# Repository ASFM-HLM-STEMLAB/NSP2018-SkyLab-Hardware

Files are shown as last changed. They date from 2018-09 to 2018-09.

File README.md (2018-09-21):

# NSP2018-SkyLab-Hardware
ASFM Near Space Program 2018 - SkyLab FlightComputer Hardware

## Welcome to NSP2018-SkyLab-Hardware repository
The flight computer consists of a *ESP32* Microcontroller in the Adafruit Feather form factor. 
[ESP32](https://www.adafruit.com/product/3405)

* Optionally we are waiting for Particle.io to release their new mesh line of MCUs. We love the development environment from Particle.io and their devices. For now we are awaiting for them to release the line, we should test compatibility when they do and hope for the best.<small>

This device contains an onboard GPS, LoRa Radio, SDCard and Internal Pressure and Temp Sensor. It is designed to interface with an optional external Iridium RockBlock Satelite Module:
[RockBlock Sat Modem](https://www.sparkfun.com/products/14498)

Also contains ports for external sensors, both in i2c and SPI. It also has a couple of mosfets for a buzzer and a beacon or optionally an electric match to prevent floaters.

See the attached BOM for details

The internal GPS is a U-Blox GPS picked because it allows the device to be effective above the 60,000ft gps limit.

Designed in Autodesk Eagle.
by: Francisco Lobo
at ASFM STEM LAB Monterrey
[HLM STEM-LAB Instagram](https://www.instagram.com/asfmstemlab/)

=======

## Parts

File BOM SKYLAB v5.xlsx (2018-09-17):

SKY LAB V5.0 - HIGH ALTITUDE BALOON MAIN COMPUTER (BOM)
https://github.com/ASFM-HLM-STEMLAB/skylab
Revision 5 | Sept 17 2018
Part | Value | Package | Part. No. | Description | PROD_ID | DigiKey URL
R3 | 10 | 603 | MCT06030C1009FP500 | Resistor |  | https://www.digikey.com/product-detail/en/vishay-beyschlag/MCT06030C1009FP500/MCT0603-10.0-CFTR-ND/2607826
R13 | 220 | M0805 | ERJ-PB6D2200V | RESISTOR, American symbol |  | https://www.digikey.com/product-detail/en/panasonic-electronic-components/ERJ-PB6D2200V/P20941TR-ND/6213724
R9 | 330 | M0805 | P330CDKR-ND | RESISTOR, American symbol |  | https://www.digikey.com/product-detail/en/panasonic-electronic-components/ERJ-6ENF3300V/P330CDKR-ND/1747213
R10 | 330 | M0805 | P330CDKR-ND | RESISTOR, American symbol |  | https://www.digikey.com/product-detail/en/panasonic-electronic-components/ERJ-6ENF3300V/P330CDKR-ND/1747213
R11 | 330 | M0805 | P330CDKR-ND | RESISTOR, American symbol |  | https://www.digikey.com/product-detail/en/panasonic-electronic-components/ERJ-6ENF3300V/P330CDKR-ND/1747213
R12 | 330 | M0805 | P330CDKR-ND | RESISTOR, American symbol |  | https://www.digikey.com/product-detail/en/panasonic-electronic-components/ERJ-6ENF3300V/P330CDKR-ND/1747213
C1 | 0.1uF | 603 | CC0603ZRY5V9BB104 | 0.1¬µF ceramic capacitors | CAP-00810 | https://www.digikey.com/product-detail/en/yageo/CC0603ZRY5V9BB104/311-1343-1-ND/2103127
C2 | 0.1uF | 603 | CC0603ZRY5V9BB104 | 0.1¬µF ceramic capacitors | CAP-00810 | https://www.digikey.com/product-detail/en/yageo/CC0603ZRY5V9BB104/311-1343-1-ND/2103127
C5 | 0.1uF | 603 | CC0603ZRY5V9BB104 | 0.1¬µF ceramic capacitors | CAP-00810 | https://www.digikey.com/product-detail/en/yageo/CC0603ZRY5V9BB104/311-1343-1-ND/2103127
C6 | 0.1uF | 603 | CC0603ZRY5V9BB104 | 0.1¬µF ceramic capacitors | CAP-00810 | https://www.digikey.com/product-detail/en/yageo/CC0603ZRY5V9BB104/311-1343-1-ND/2103127
C4 | 10uF | 1206 | CL31A106KPHNNNE | 10.0¬µF ceramic capacitors | CAP-10057 | https://www.digikey.com/product-detail/en/samsung-electro-mechanics/CL31A106KPHNNNE/1276-1148-1-ND/3889234
R8 | 220K | 805 | KTR10EZPF2203 | 0.22Œ© resistor | RES-09883 | https://www.digikey.com/product-detail/en/rohm-semiconductor/KTR10EZPF2203/RHM220KAHCT-ND/1983969
R14 | 220K | 805 | KTR10EZPF2203 | 0.22Œ© resistor | RES-09883 | https://www.digikey.com/product-detail/en/rohm-semiconductor/KTR10EZPF2203/RHM220KAHCT-ND/1983969
C8 | 22uF | 805 | CL21A226KPCLRNC | 22¬µF ceramic capacitors | CAP-08402 | https://www.digikey.com/product-detail/en/samsung-electro-mechanics/CL21A226KPCLRNC/1276-6786-6-ND/5962020
D3 | 250mA/100V | SOD-323 | 1N4148WSF | Diode 250mA/100V | DIO-09646 | https://www.digikey.com/product-detail/en/diodes-incorporated/1N4148WSF-7/1N4148WSF-7DICT-ND/7605263
R7 | 2M | 805 | RC0805FR-072ML | 0.22Œ© resistor | RES-09883 | https://www.digikey.com/product-detail/en/yageo/RC0805FR-072ML/311-2.00MCRCT-ND/730612
R15 | 2M | 805 | RC0805FR-072ML | 0.22Œ© resistor | RES-09883 | https://www.digikey.com/product-detail/en/yageo/RC0805FR-072ML/311-2.00MCRCT-ND/730612
C3 | 330uF | EIA6032 | TPSC337K006R0080 | Capacitor Polarized |  | https://www.digikey.com/product-detail/en/TPSC337K006R0080/478-11108-1-ND/7536284
L1 | 33nH | 603 | LQW18AN33NJ00D | Inductors |  | https://www.digikey.com/product-detail/en/murata-electronics-north-america/LQW18AN33NJ00D/490-1175-1-ND/584620
R1 | 4.7K | M0805 | ESR10EZPJ472 | RESISTOR, American symbol |  | https://www.digikey.com/product-detail/en/rohm-semiconductor/ESR10EZPJ472/RHM4.7KKCT-ND/1763028
R2 | 4.7K | M0805 | ESR10EZPJ472 | RESISTOR, American symbol |  | https://www.digikey.com/product-detail/en/rohm-semiconductor/ESR10EZPJ472/RHM4.7KKCT-ND/1763028
R4 | 4.7K | M0805 | ESR10EZPJ472 | RESISTOR, American symbol |  | https://www.digikey.com/product-detail/en/rohm-semiconductor/ESR10EZPJ472/RHM4.7KKCT-ND/1763028
R5 | 4.7K | M0805 | ESR10EZPJ472 | RESISTOR, American symbol |  | https://www.digikey.com/product-detail/en/rohm-semiconductor/ESR10EZPJ472/RHM4.7KKCT-ND/1763028
R6 | 4.7K | M0805 | ESR10EZPJ472 | RESISTOR, American symbol |  | https://www.digikey.com/product-detail/en/rohm-semiconductor/ESR10EZPJ472/RHM4.7KKCT-ND/1763028
R16 | 4.7K | M0805 | ESR10EZPJ472 | RESISTOR, American symbol |  | https://www.digikey.com/product-detail/en/rohm-semiconductor/ESR10EZPJ472/RHM4.7KKCT-ND/1763028
L2 | 4.7uH 1.2A | 603 | MBKK1608T4R7M | Inductors |  | https://www.digikey.com/product-detail/en/taiyo-yuden/MBKK1608T4R7M/587-4152-1-ND/5035312
Q2 | 5.8A/30V/35mŒ | SOT23-3 | SSM3K333R,LF | N-channel MOSFETs | TRANS-12988 | https://www.digikey.com/product-detail/en/toshiba-semiconductor-and-storage/SSM3K333RLF/SSM3K333RLFCT-ND/3522391
Q1 | 500mA/300V | SOT23-3 | ZXTN19020DFFTA | NPN transistor | TRANS-09116 | https://www.digikey.com/product-detail/en/diodes-incorporated/ZXTN19020DFFTA/ZXTN19020DFFCT-ND/1557774
BT1 | 6.8MM_CELL | BATT-6.8MM | MS621FE-FL11E | Battery - Single Cell | BATT-13734 | https://www.digikey.com/product-detail/en/seiko-instruments/MS621FE-FL11E/728-1057-ND/1889208
U2 | BME680 | LGA3.0X3.0 | BME680 | BME 680 - Sensor |  | https://www.digikey.com/product-detail/en/bosch-sensortec/BME680/828-1077-1-ND/7401321
LED | Green | LED-1206 | LTST-C150GKT‎ | LED (Generic) |  | https://www.digikey.com/product-detail/en/lite-on-inc/LTST-C150GKT/160-1169-1-ND/269241
LED | Green | LED-1206 | LTST-C150GKT‎ | LED (Generic) |  | https://www.digikey.com/product-detail/en/lite-on-inc/LTST-C150GKT/160-1169-1-ND/269241
LED | Green | LED-1206 | LTST-C150GKT‎ | LED (Generic) |  | https://www.digikey.com/product-detail/en/lite-on-inc/LTST-C150GKT/160-1169-1-ND/269241
LED | Green | LED-1206 | LTST-C150GKT‎ | LED (Generic) |  | https://www.digikey.com/product-detail/en/lite-on-inc/LTST-C150GKT/160-1169-1-ND/269241
J2 | SD_SOCKET | SD_SOCKET | 5031821852 | microSD Socket for Transflash | CONN-07820 | https://www.digikey.com/product-detail/en/molex-llc/5031821852/WM12834CT-ND/5823232
RADIO | RFM95W | RFM95W | RFM95W-915S2-ND | LoRA Radio |  | https://www.digikey.com/product-detail/en/rf-solutions/RFM95W-915S2/RFM95W-915S2-ND/6564923
GPS_ANT | SMA_EDGE | SMA-EDGE | 132255RP | SMA Antenna Connector |  | https://www.digikey.com/product-detail/en/amphenol-rf-division/132255RP/ACX1425-ND/1989874
RDIO_ANT | SMA_EDGE | SMA-EDGE | CON-SMA-EDGE-S | SMA Antenna Connector |  | https://www.digikey.com/product-detail/en/rf-solutions/CON-SMA-EDGE-S/CON-SMA-EDGE-S-ND/5845767
U1 | TPS61200 | QFN-10_PAD | TPS61200DRCT | DC to DC Booster | IC-10035 | https://www.digikey.com/product-detail/en/texas-instruments/TPS61200DRCT/296-21663-1-ND/1534252
UBLOX | UBLOX_MAX | UBLOX_MAX | MAX-M8W-0 | UBLOX MAX |  | https://www.digikey.com/product-detail/en/u-blox-america-inc/MAX-M8W-0/672-1004-1-ND/6150667
J1 |  | JST-2-SMD | S2B-PH-SM4-TB(LF)(SN) | JST 2MM MALE RA CONNECTOR | CONN-11443 | https://www.digikey.com/product-detail/en/jst-sales-america-inc/S2B-PH-SM4-TB-LF-SN/455-1749-1-ND/926846
S1 |  | SWTCH | PCM12SMTR | Single Pole, Double Throw (SPDT) Switch | SWCH-10651 | https://www.digikey.com/product-detail/en/c-k/PCM12SMTR/401-2016-1-ND/1640125

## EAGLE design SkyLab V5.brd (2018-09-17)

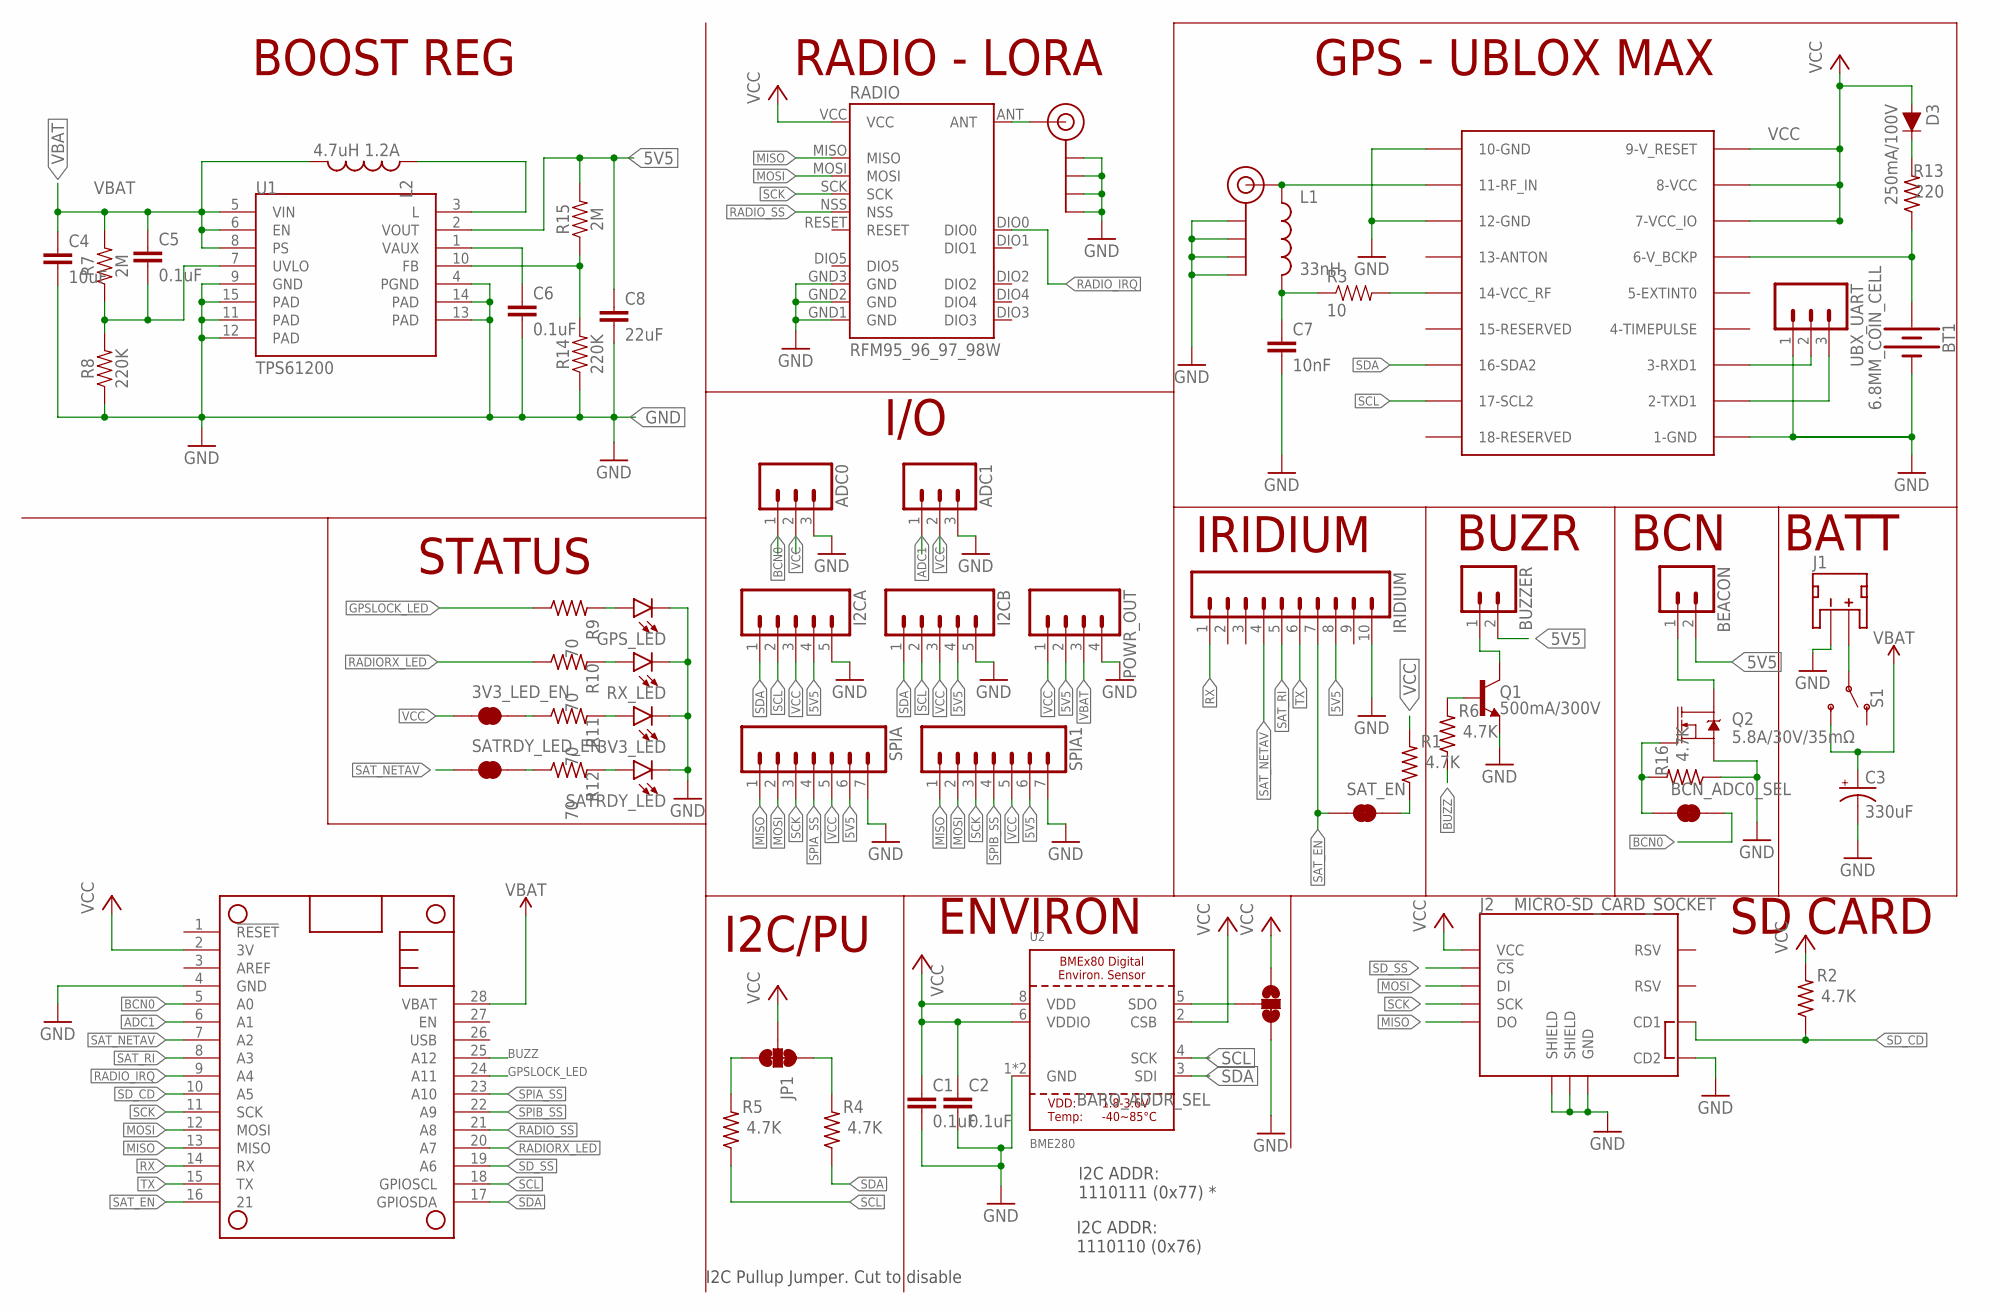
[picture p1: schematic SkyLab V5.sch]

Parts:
3V3_LED: LED1206; LED-1206
3V3_LED_EN: JUMPER-SMT_2_NC_TRACE_SILK; SMT-JUMPER_2_NC_TRACE_SILK
ADC0, ADC1: CONN_03; 1X03
BARO_ADDR_SEL: JUMPER-SMT_3_1-NC_TRACE_SILK; SMT-JUMPER_3_1-NC_TRACE_SILK
BCN_ADC0_SEL: JUMPER-SMT_2_NC_TRACE_SILK; SMT-JUMPER_2_NC_TRACE_SILK
BEACON: CONN_02; 1X02
BT1: 6.8MM_COIN_CELL; BATTCON-6.8MM
BUZZER: CONN_02; 1X02
C1, C2, C5, C6: 0.1uF; 0603
C3: 330uF; EIA6032
C4: 10uF; 1206
C7: 10nF; 0603
C8: 22uF; 0805
D3: 250mA/100V; SOD-323
GPS_ANT: SMA_EDGE; SMA-EDGE
GPS_LED: LED1206; LED-1206
I2CA, I2CB: CONN_05; 1X05
IRIDIUM: CONN_10"; 1X10
J1: JST_2MM_MALE; JST-2-SMD
J2: MICRO-SD_CARD_SOCKET; MICRO-SD-SOCKET
JP1: JUMPER-SMT_3_2-NC_TRACE_SILK; SMT-JUMPER_3_2-NC_TRACE_SILK
L1: 33nH; 0603
L2: 4.7uH 1.2A; 0603
MS1: FEATHERWING_NODIM; FEATHERWING_DIM
POWR_OUT: CONN_04; 1X04
Q1: 500mA/300V; SOT23-3
Q2: 5.8A/30V/35mΩ; SOT23-3
R1, R2, R4, R5, R6, R16: 4.7K; M0805
R3: 10; 0603-RES
R7, R15: 2M; 0805
R8, R14: 220K; 0805
R9, R10, R11, R12: 70; M0805
R13: 220; M0805
RADIO: RFM95_96_97_98W
RDIO_ANT: SMA_EDGE; SMA-EDGE
RX_LED: LED1206; LED-1206
S1: SWITCH-SPDT-SMD-RIGHT-ANGLE; SWITCH_SPST_SMD_A
SATRDY_LED: LED1206; LED-1206
SATRDY_LED_EN: JUMPER-SMT_2_NC_TRACE_SILK; SMT-JUMPER_2_NC_TRACE_SILK
SAT_EN: JUMPER-SMT_2_NC_TRACE_SILK; SMT-JUMPER_2_NC_TRACE_SILK
SPIA, SPIA1: CONN_07; 1X07
U1: TPS61200; QFN-10_PAD
U2: BME280
UBLOX: UBLOX_MAX
UBX_UART: CONN_03; 1X03

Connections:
5V5: BEACON.2, BUZZER.2, C8.1, I2CA.4, I2CB.4, IRIDIUM.8, POWR_OUT.2, R15.2, SPIA.6, SPIA1.6, U1.2 (VOUT)
ADC1: ADC1.1, MS1.6 (A1)
BCN0: ADC0.1, BCN_ADC0_SEL.2, MS1.5 (A0)
BUZZ: MS1.25 (A12), R6.1
EDITINF: BCN_ADC0_SEL.1, Q2.1 (G), R16.2
GND: 3V3_LED.C, ADC0.3, ADC1.3, BARO_ADDR_SEL.3, BT1.-, C1.2, C2.2, C3.P$2 (-), C4.2, C6.2, C7.2, C8.2, GPS_ANT.GND@0 (GND), GPS_ANT.GND@1 (GND), GPS_ANT.GND@2 (GND), GPS_ANT.GND@3 (GND), GPS_LED.C, I2CA.5, I2CB.5, IRIDIUM.10, J1.1 (-), J2.CD2, J2.GND, J2.GND1 (SHIELD), J2.GND3 (SHIELD), MS1.4 (GND), POWR_OUT.4, Q1.2 (E), Q2.2 (S), R8.1, R14.1, R16.1, RADIO.GND1 (GND), RADIO.GND2 (GND), RADIO.GND3 (GND), RDIO_ANT.GND@0 (GND), RDIO_ANT.GND@1 (GND), RDIO_ANT.GND@2 (GND), RDIO_ANT.GND@3 (GND), RX_LED.C, SATRDY_LED.C, SPIA.7, SPIA1.7, U1.4 (PGND), U1.9 (GND), U1.11 (PAD), U1.12 (PAD), U1.13 (PAD), U1.14 (PAD), U1.15 (PAD), U2.1 (GND), U2.7 (GND), UBLOX.1-GND, UBLOX.10-GND, UBLOX.12-GND, UBX_UART.1
GPSLOCK_LED: MS1.24 (A11), R9.1
MISO: J2.DO, MS1.13 (MISO), RADIO.MISO, SPIA.1, SPIA1.1
MOSI: J2.DI, MS1.12 (MOSI), RADIO.MOSI, SPIA.2, SPIA1.2
unnamed: R1.1, SAT_EN.2
unnamed: GPS_ANT.SIG (SIGNAL), L1.1, UBLOX.11-RFIN (11-RF_IN)
unnamed: C7.1, L1.2, R3.1
unnamed: R3.2, UBLOX.14-VCC_RF
unnamed: RADIO.ANT, RDIO_ANT.SIG (SIGNAL)
unnamed: JP1.3, R5.2
unnamed: JP1.1, R4.2
unnamed: Q1.1 (B), R6.2
unnamed: BUZZER.1, Q1.3 (C)
unnamed: GPS_LED.A, R9.2
unnamed: BT1.+, R13.1, UBLOX.6-V_BCKP
unnamed: R12.1, SATRDY_LED_EN.2
unnamed: R10.2, RX_LED.A
unnamed: 3V3_LED.A, R11.2
unnamed: 3V3_LED_EN.2, R11.1
unnamed: D3.C, R13.2
unnamed: BARO_ADDR_SEL.2, U2.5 (SDO)
unnamed: R12.2, SATRDY_LED.A
unnamed: C5.2, R7.1, R8.2, U1.7 (UVLO)
unnamed: UBLOX.3-RXD1, UBX_UART.2
unnamed: UBLOX.2-TXD1, UBX_UART.3
unnamed: R14.2, R15.1, U1.10 (FB)
unnamed: L2.1, U1.3 (L)
unnamed: C6.1, U1.1 (VAUX)
unnamed: BEACON.1, Q2.3 (D)
RADIORX_LED: MS1.20 (A7), R10.1
RADIO_IRQ: MS1.9 (A4), RADIO.DIO0
RADIO_SS: MS1.21 (A8), RADIO.NSS
RX: IRIDIUM.1, MS1.14 (RX)
SAT_EN: IRIDIUM.7, MS1.16 (21), SAT_EN.1
SAT_NETAV: IRIDIUM.4, MS1.7 (A2), SATRDY_LED_EN.1
SAT_RI: IRIDIUM.5, MS1.8 (A3)
SCK: J2.SCLK (SCK), MS1.11 (SCK), RADIO.SCK, SPIA.3, SPIA1.3
SCL: I2CA.2, I2CB.2, MS1.18 (GPIOSCL), R5.1, U2.4 (SCK), UBLOX.17-SCL2
SDA: I2CA.1, I2CB.1, MS1.17 (GPIOSDA), R4.1, U2.3 (SDI), UBLOX.16-SDA2
SD_CD: J2.CD1, MS1.10 (A5), R2.1
SD_SS: J2.CS (!CS), MS1.19 (A6)
SPIA_SS: MS1.23 (A10), SPIA.4
SPIB_SS: MS1.22 (A9), SPIA1.4
TX: IRIDIUM.6, MS1.15 (TX)
VBAT: C3.P$1 (+), C4.1, C5.1, L2.2, MS1.28 (VBAT), POWR_OUT.3, R7.2, S1.3 (S), U1.5 (VIN), U1.6 (EN), U1.8 (PS)
VBAT_SUPPLY: J1.2 (+), S1.2
VCC: 3V3_LED_EN.1, ADC0.2, ADC1.2, BARO_ADDR_SEL.1, C1.1, C2.1, D3.A, I2CA.3, I2CB.3, J2.VCC, JP1.2, MS1.2 (3V), POWR_OUT.1, R1.2, R2.2, RADIO.VCC, SPIA.5, SPIA1.5, U2.2 (CSB), U2.6 (VDDIO), U2.8 (VDD), UBLOX.7-VCC_IO, UBLOX.8-VCC, UBLOX.9-V_RESET

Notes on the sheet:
GPS - UBLOX MAX
BOOST REG
RADIO - LORA
IRIDIUM
I/O
BUZR
BATT
I2C/PU
I2C Pullup Jumper. Cut to disable
I2C ADDR: 1110110 (0x76)
I2C ADDR: 1110111 (0x77) *
ENVIRON
SD CARD
STATUS
BCN

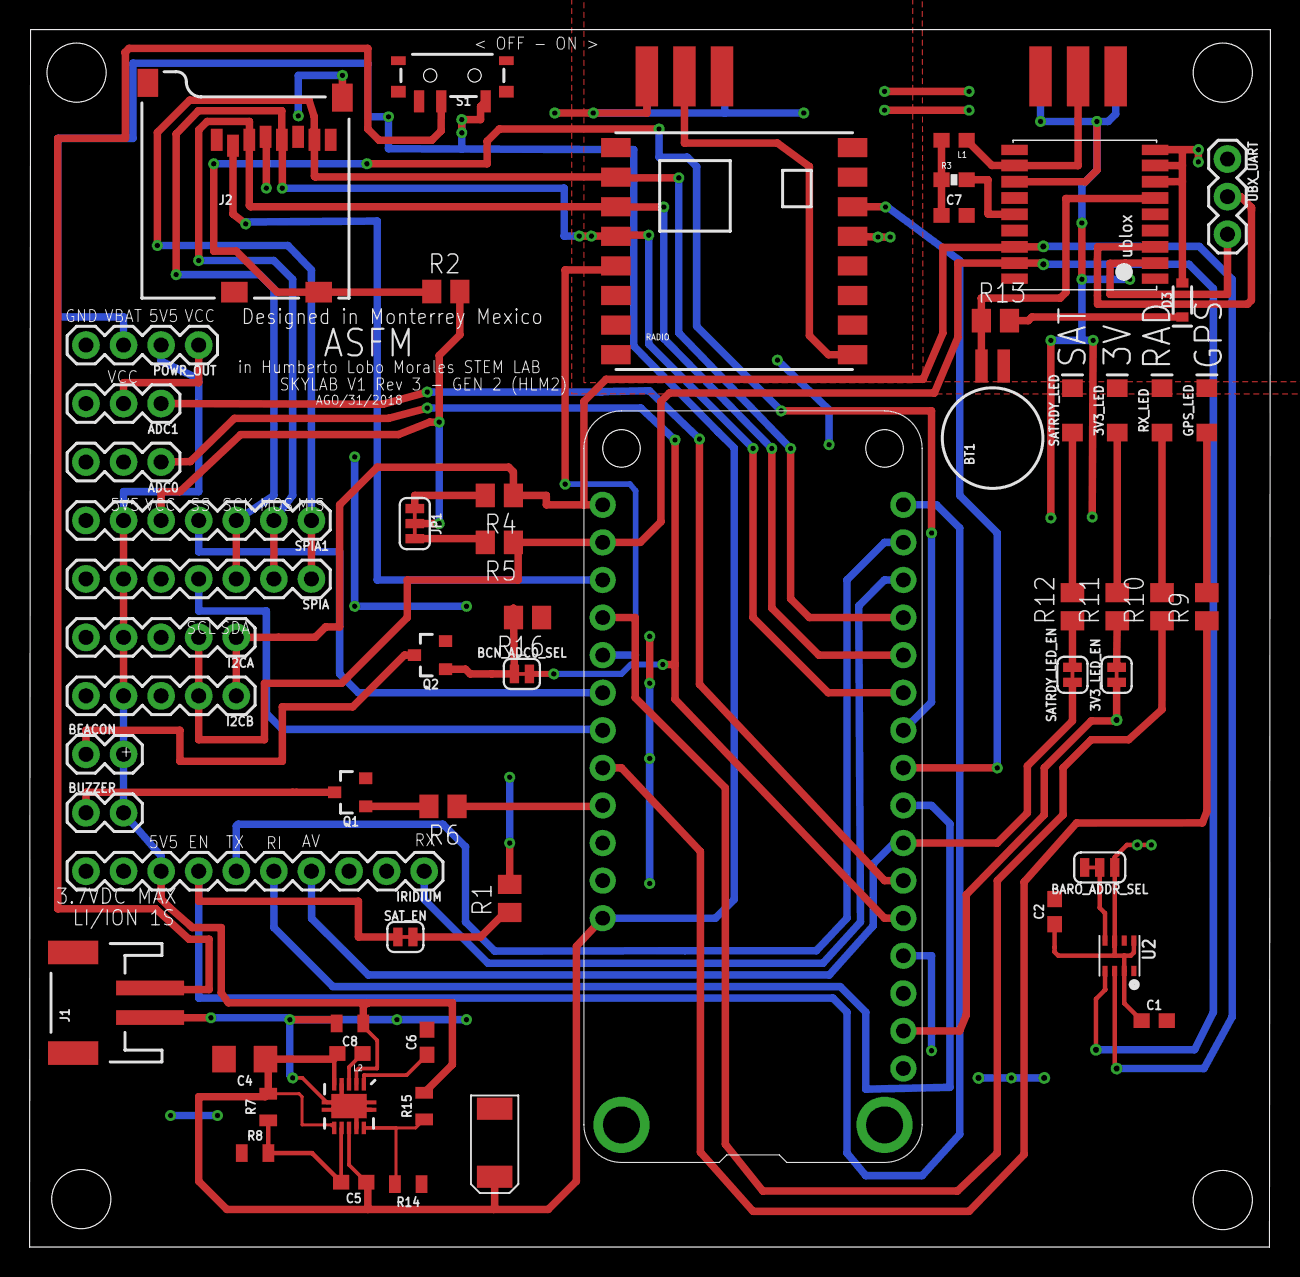
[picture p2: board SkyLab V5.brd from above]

Board: 2 copper layers, 83.9 x 82.3 mm, 61 parts (0 on the bottom side), 52 nets.

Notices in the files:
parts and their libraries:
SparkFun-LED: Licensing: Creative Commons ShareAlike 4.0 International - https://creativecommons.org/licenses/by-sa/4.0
